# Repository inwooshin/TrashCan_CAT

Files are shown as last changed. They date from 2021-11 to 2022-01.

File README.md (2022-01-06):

# Trash Can   

## 목차    
[1. 개요](#개요)   
[2. 발표영상](#발표영상)   
[3. 사용 CPU 및 센서](#사용-cpu-및-센서)   
[4. 구조 설계](#구조-설계)   
[5, 사용 STL 도면](#사용-stl-도면)   
[6. 외형](#외형)   
[7. 시연 영상](#시연-영상)   
[8. 조원별 역할](#조원별-역할)   

## 개요

push_pull

이 프로젝트는 압축 기능 및 IoT 기능을 사용할 수 있는 쓰레기통인 C.A.T(Can do Anything Trash can) 에 관한 프로젝트이다. WiFi 라이브러리를 사용하고 HTTP 로 ESP8266 과 앱인벤터의 통신이 가능하도록 설계하였다. 그리고 STL 파일으로 Press Hardware 를 수정하여 Scissors Linkage 의 구조로 3D 프린팅 하였으며, Torque 가 부족하기 때문에 기존의 gear 를 1개에서 2개로 사용을 변경하여 Push 와 Pull 이 용이하게 만들었다.
   
## 발표영상
발표영상화면 (https://www.youtube.com/watch?v=RVP99xg6Qa0)   
위의 사진을 클릭하시면 Youtube 링크로 이동합니다.   

## 사용 CPU 및 센서

- **ESP8266**
    
    esp
    
    1. 전체 GPIO 핀을 제어하기 위한 메인보드
    2. Application과 연결하기 위한 WiFi 모듈 내장
    3. 3.3V Power Logic
- **12V Motor Driver**
    
    MotorDriver
    
    1. PWM을 통해서 모터속도 제어 가능
    2. 정전압 역전압으로 양방향 제어 가능
    3. 입력 전압 : 5 ~ 35 V / 동작 전압 : 5V
- **Pololu 50:1 Metal Gearmotor 12V**
    
    gear
)
    
    1. Rack - Pinion 을 구동하기 위한 DC Motor
    2. 구동전압 : 12V / RPM : 200 / Stall Torque : 21kg*cm
    / 정격 설계 : 4.2kg*cm
- **MP3 Module & Speaker**
    
    speaker
    
    1. 3W 전력 / 4Ω Impedance / 직경 : 50mm
    2. 최대 255개의 파일 저장 가능 / 30 Volume Level / 24bit DAC Output
- **DC-DC Convertor**
    
    conv
    
    1. 전원의 12V를 Node MCU 5V 정격 전압으로 강하
    2. 입력 전압 7V ~ 26V / 출력 전압 : 5V / 출력 전류 : 최대 3A
    변환 효율 : 최대 96%
- **단면 PCB 기판**
    
    pcb
    
    1. 브레드 보드를 대체하여 사용
    2. 메인보드 및 각 센서를 납땜하여 사용
- **아크릴 판**
    
    아크릴
    
    1. 본 프로젝트의 외형을 구현, 도면에 따라 재단해서 사용
    - 강판 두께 : 3T(3mm) / 강판 크기 : 500(mm)x500(mm)
- **SR - 04 초음파 센서**
    
    cho
)
    
    1. 동작전압 : 5V / 동작전류 : 15mA / 동작 주파수 : 40Hz
    발생 주파수 : 40kHz / 측정거리 : 2~400cm / 감지각도 : 15
    크기 : 45 x 20 x 15(mm)
- **12V 건전지**
    
    12v
    
    1. 8개입 건전지 CASE를 이용해 [1.5V x 8] 개 12V 전압 입력
- **SG-90**
    
    servo
    
    1. 쓰레기 투입구를 자동으로 열기 위한 Motor
    2. 각도를 0 ~ 180로 변화시키면서 연결된 Wire를 통해 문을 개폐
    3. - Weight : 9g / Torque : 1.3kg*cm(at 4.8V) / RPM : 110

### 구조 설계

- **Hardware**
    - **Scissors Linkage**
        
        ScissorsMechan
        
        구조는 Scissors Mechanism 의 구조로 설계하였다. 위에 부착해서 프레스를 해줘야하는 구조상 크기를 최대한 키우지 않을 수 있게 다리를 안으로 접을 수 있는 구조인 Scissors Mechanism 을 선택했다. 
        
    - **외형 설계**
        
        외형설계
        
    - **회로 설계**
        
        회로설계
        
- **Software**
    - ESP8266 Code (C++)
        
        12V 의 전원을 인가하게 되면 5V 로 변경시켜주는 레귤레이터를 통해서 ESP 8266 이 동작하게 된다. 그 ESP8266 에 달린 입구 부분의 초음파 센서를 확인해서 인접한 거리에 사람이 20Cm 내에 있는지 확인한다. 그리고 내에 있을 경우 입구를 오픈합니다. 또한 쓰레기의 잔량을 확인할 수 있도록 압축 판에 부착한 초음파센서가 쓰레기의 잔량을 재서 20Cm 보다 작으면 압축 동작을 시킬 수 있도록 하였다. 그리고 앱인벤터의 신호를 확인해서 들어오는 Open 이나 Press 그리고 Remain check 같은 잔량 체크를 하는 동작을 수행할 수 있도록 하였다.
        
        소프트웨어플로우차트
        
    - App Inventor
        
        우선 HTTP 의 GET 을 통해서 Compression 의 PRESS 라는 키워드를 넣어서 접속할 경우 해당 키워드에 접속을 주시하고 있던 ESP8266 이 Press 동작을 수행한다. 그리고 이 동작을 한 후 응답을 보내 온전하게 연결이 되고 동작을 수행했는지를 알 수 있도록 하였다. 이 형식으로 Remain check, 딜레이 시간을 조정하는 push 와 pull 의 딜레이 시간을 조정할 수 있도록 하였다.
        
        앱인벤터플로우차트

### 사용 STL 도면

- Linkage 상하단 구조물

stl-1

[https://www.thingiverse.com/thing:3483911](https://www.thingiverse.com/thing:3483911) 의 Scissors Mechanism 도면을 사용하였다. 기존의 것과 다른 것은 아래의 Second Gear 구조물의 Pinion Gear 와 Linkage 상단의 Rack Gear 의 align 을 맞출 수 있도록 수정하였다.

- Second Gear 구조물

stl-2

[https://www.thingiverse.com/thing:677144](https://www.thingiverse.com/thing:677144) 의 도면을 수정하여 사용하였다. 원도면과 Second Gear Holder 가 굉장히 다른 모양이다. 이것은 Linkage 의 도면과 부착하는 부분이 없기 때문에 고정해줄 수 있는 부분을 만들어서 부착해주었고 두번째 기어를 고정하는 부분을 위로 Shift 시켜서 수정했기 때문이다. 그리고 부족한 토크로인한 기어비를 3:1 로 최대로 주기 위해서 조금 더 수정하고 기어와의 align 을 수정하였다.

## 외형

- 정면
    
    전면
    
- 후면
    
    후면

- 측면
    
    측면

## 시연 영상

- Push n Pull

push_pull   
- 앱인벤터로 Press n Pull

앱인벤터푸시

- 외부 사용자 감지 시

open

- 쓰레기통 남은량 감지
    - 전부 비어있을 때
    
    remainCheck_full
    
    - 조금만 차있을 때
    
    remainCheck_half

## 조원별 역할

- 신인우(조장)
    - 전체 코드 구현
    - 하드웨어 설계
    - 부품 선정
    - STL 도면 수정
- 김홍민
    - 하드웨어 설계
    - 부품 선정
    - 외형 설계
    - 음성파일 제작
- 유건환
    - 외형 설계
    - PCB 납땜
    - 외형에 하드웨어 부착
    - 앱인벤터 제작

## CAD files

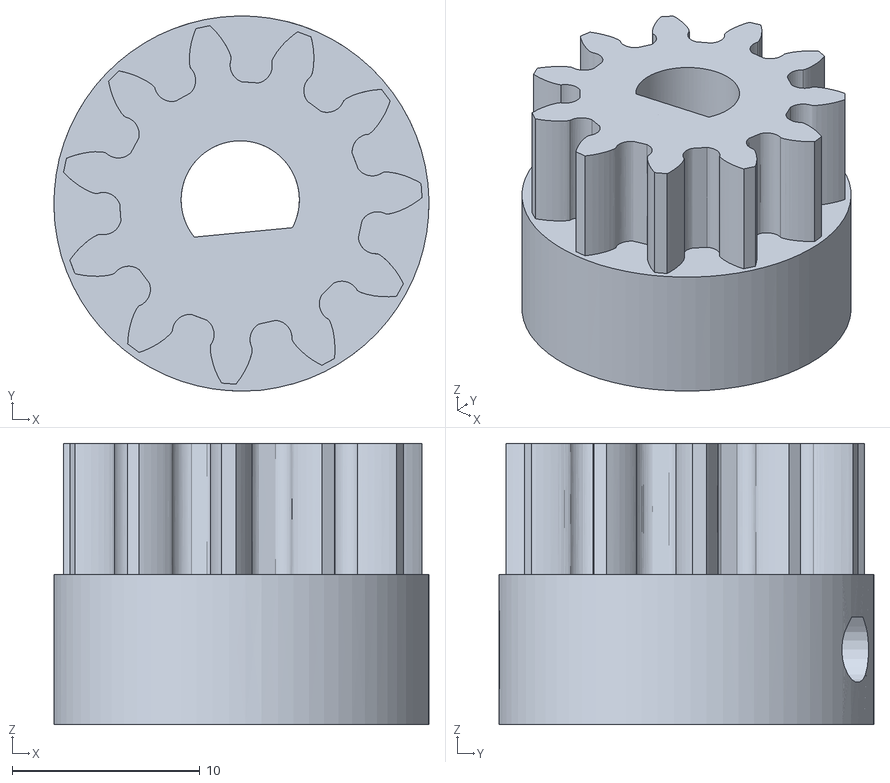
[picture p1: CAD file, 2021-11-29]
stl/wide_small_gear.stl
20.0 x 20.0 x 15.0

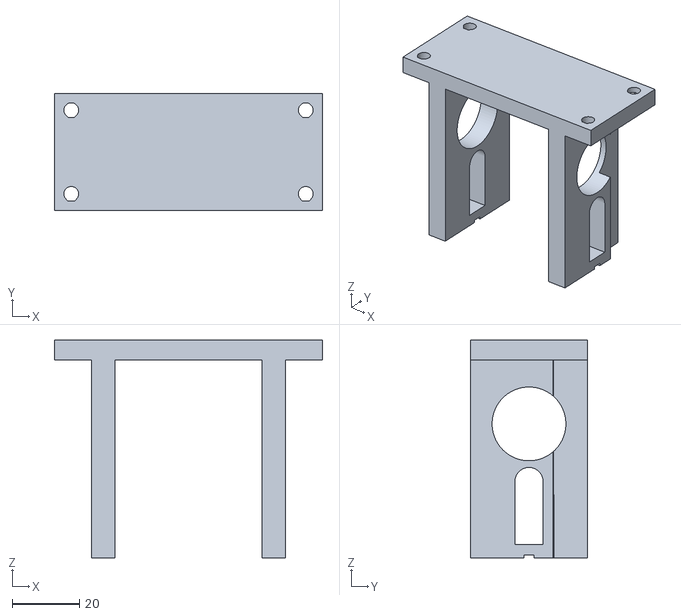
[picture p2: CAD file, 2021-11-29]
stl/Top.stl
80.0 x 35.0 x 65.0

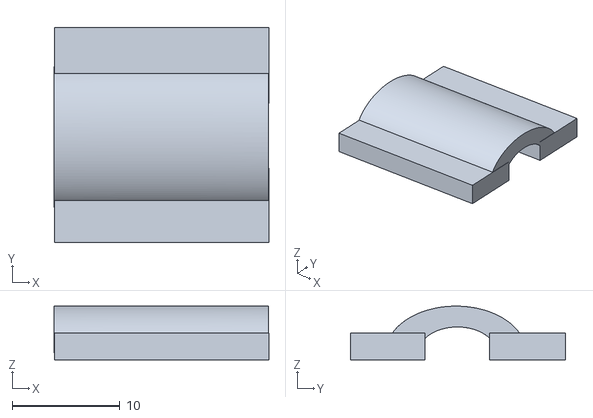
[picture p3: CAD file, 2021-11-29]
stl/thread.stl
20.0 x 20.0 x 5.00

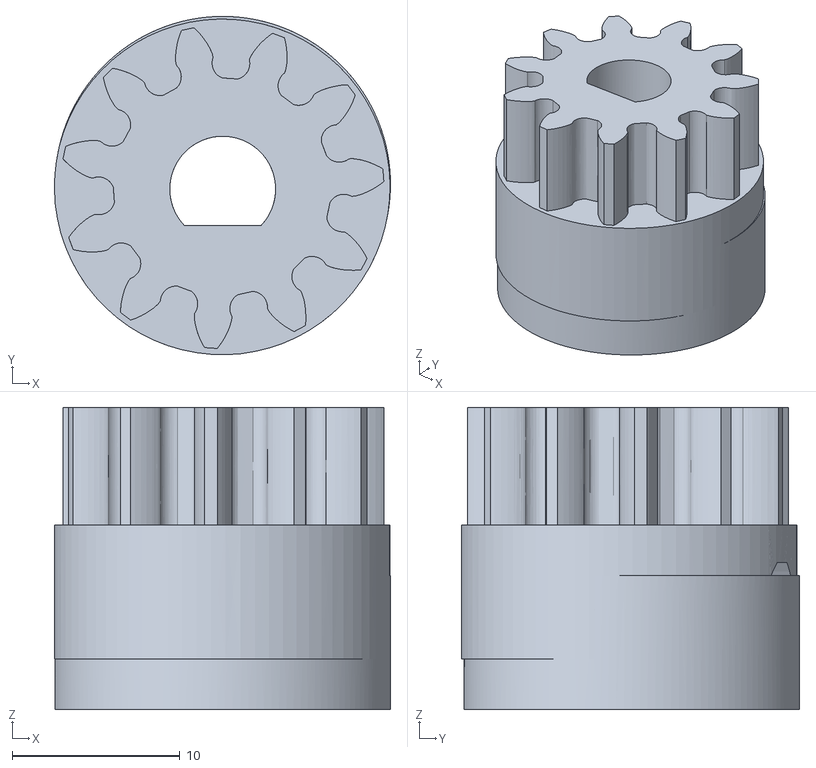
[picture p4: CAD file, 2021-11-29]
stl/small_gear_upversion.stl
20.0 x 20.2 x 18.0

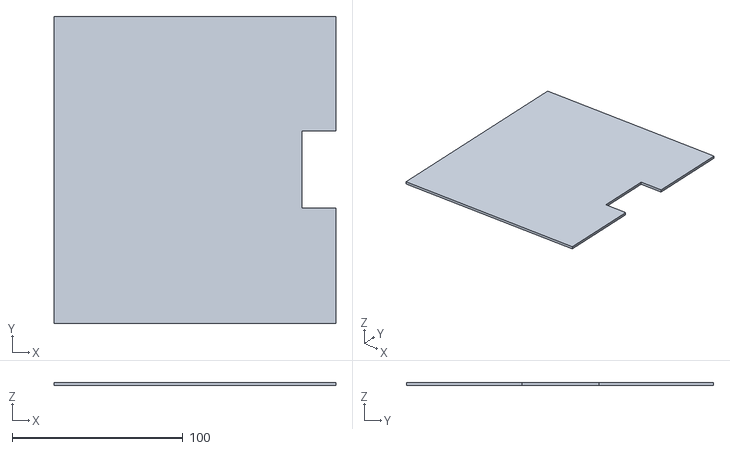
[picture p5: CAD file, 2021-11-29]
stl/press_board.stl
165.1 x 180.0 x 2.00

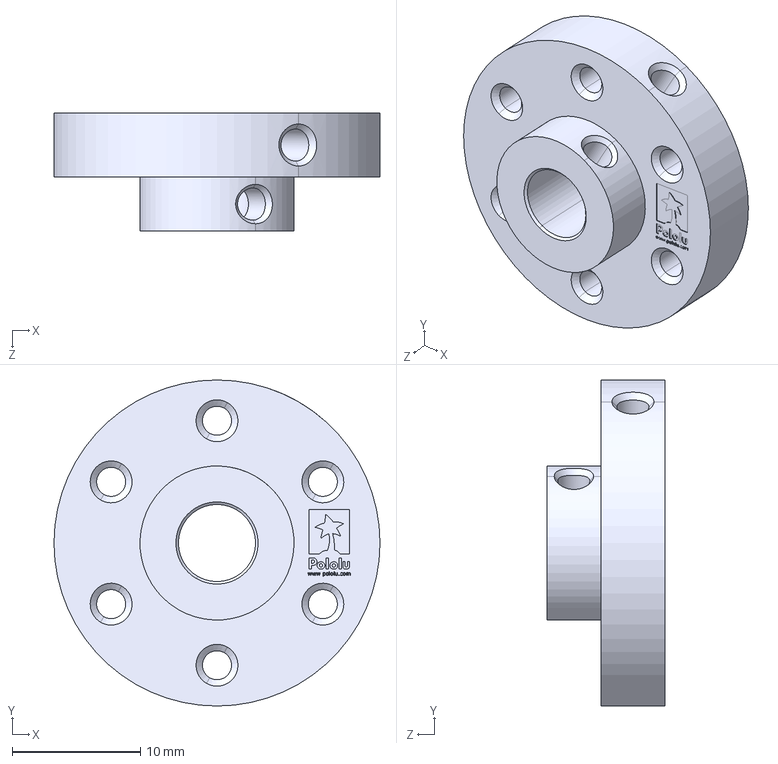
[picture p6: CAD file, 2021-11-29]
stl/pololu-universal-aluminum-mounting-hub-for-6mm-shaft-4-40-holes.step
25.4 x 25.4 x 9.20 mm

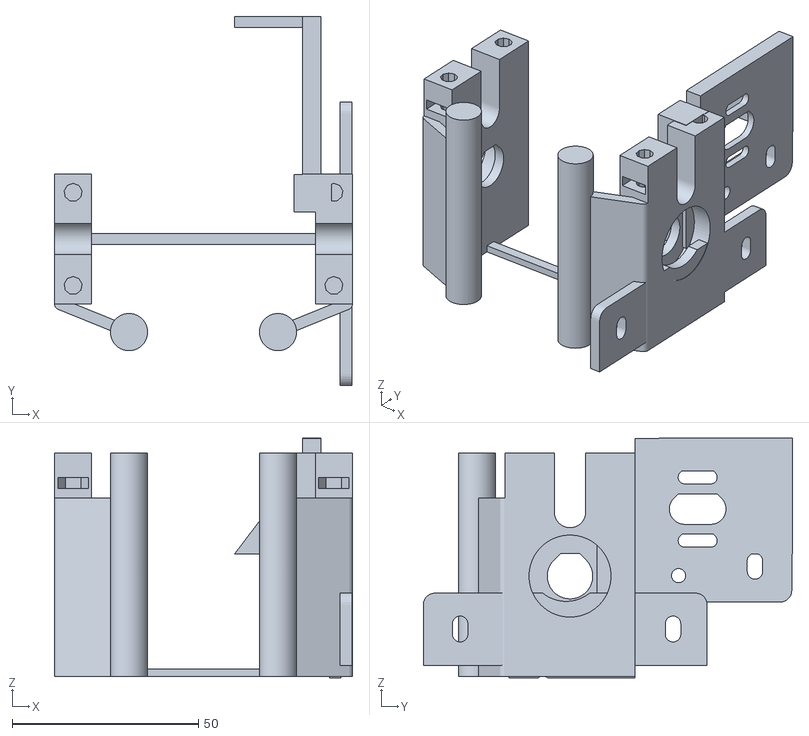
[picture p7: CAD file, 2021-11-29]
stl/newGearHolder.stl
80.0 x 99.2 x 64.3

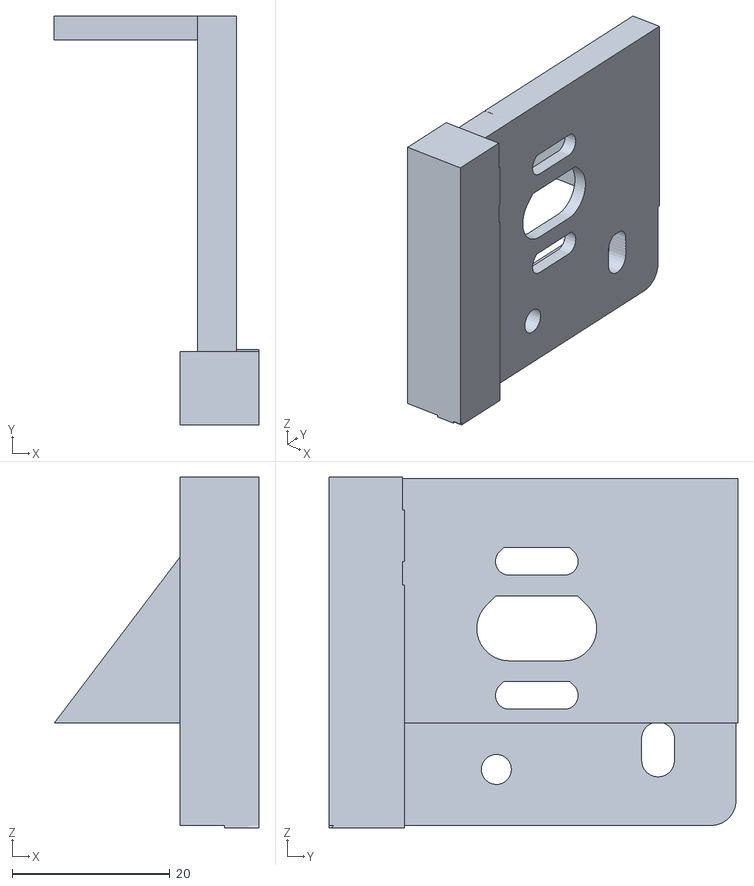
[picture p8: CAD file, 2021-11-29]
stl/floatingGearHolder.stl
25.9 x 51.9 x 44.5

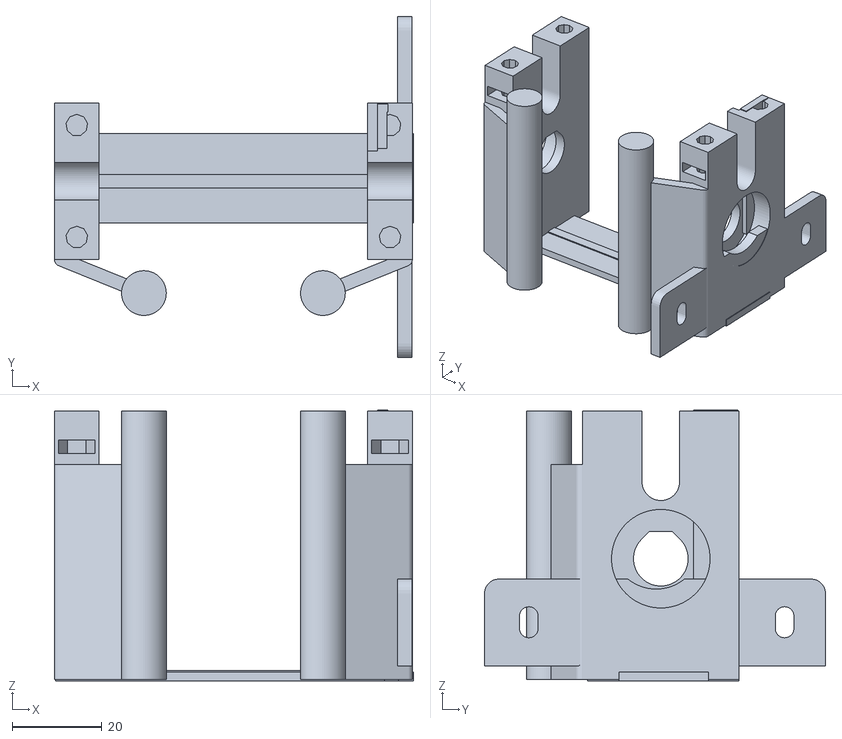
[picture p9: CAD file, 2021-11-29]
stl/braket_one_gear.stl
80.3 x 76.2 x 60.5

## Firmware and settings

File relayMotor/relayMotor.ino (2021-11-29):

#include "Servo.h"
#define RelayPlusPin D1
#define RelayMinusPin D2
#include "SoftwareSerial.h"
#include "DFRobotDFPlayerMini.h"
#include <ESP8266WiFi.h>
#include <ESP8266HTTPClient.h>

//openECHO 나중에 바꿔야함!!

int pushTRIG = D7;    // 트리거 핀 선언
int pushECHO = D6;    // 에코 핀 선언
int openTRIG = D4;    // SD3 나중에 바꿔야함
int openECHO = D5;
int servoPin = D8;

//확정
int servoStart = 0, servoEnd = 90, servoDelay = 5000;

//D3,4-> D4에서 input 으로 설정해주면 에러가 나는 것 같다!(input 설정이 안되는 듯)
//D3 도 output trig 했는데 안됨
//빨강이 위, 갈색이 아래

//
int Clock = 1, pushDelayTime = 230, pullDelayTime = 335, count = 0;
int pushPower = 900, pullPower = 1020;
int distanceDelayTime = 100;
int vol = 25;

const char *ssid = "INS_phone";
const char *password = "kkkkkkkk";

IPAddress ip (192, 168, 119, 101); // 연결할, 고정 IP 주소
IPAddress gateway (192, 168, 119, 135); // 게이트웨이 주소
IPAddress subnet (255, 255, 255, 0); // 서브마스크 주소
WiFiServer server(80);
WiFiClient client;
Servo myServo;

SoftwareSerial mySoftwareSerial(3, 1); // RX, TX
DFRobotDFPlayerMini myDFPlayer;

int countDistance(int modeChoice, int runMode);

//모터 동작 멈추기
void stop(){
  digitalWrite(RelayPlusPin, LOW);
  digitalWrite(RelayMinusPin, LOW);  
}

//모터 press
void push(){
  analogWrite(RelayPlusPin,1024);
  digitalWrite(RelayMinusPin,LOW); // 회전
  delay(pushDelayTime);
  stop();
}

//모터 pull
void pull(){
  digitalWrite(RelayPlusPin,LOW); 
  analogWrite(RelayMinusPin,1024);
  delay(pullDelayTime);
  stop();
}

//모터 사이클 동작
void motorCycle(){
  //push 음성안내 음성 출력
  myDFPlayer.play(1);
  delay(2500);
  Serial.println("push");
  push();
      
  delay(2000);
  
  //pull 음성안내 출력
  myDFPlayer.play(2);
  delay(1000);
  Serial.println("pull");
  pull();
}

void servoRun(){
  //문 Open 음성안내 출력
  myDFPlayer.play(4);
  
  myServo.write(servoStart);
  delay(servoDelay);
  myServo.write(servoEnd);
}

int countDistance(int modeChoice, int runMode){
  //modeChoice - mode == 0 -> push 거리, mode == 1 open 거리
  //runMode - runMode == 0 -> 작동 x, runMode == 1 -> 작동 o
  int TRIG = 0, ECHO = 0;
  
  //
  if(modeChoice == 0){ 
    Serial.println("press Distance");
    TRIG = pushTRIG;
    ECHO = pushECHO;
  }
  else{ 
    Serial.println("Open Distance");
    TRIG = openTRIG;
    ECHO = openECHO;
  }
  
  //open 일 경우 0, press 일 경우 1
  long duration, distance;
  digitalWrite(TRIG, LOW);
  delayMicroseconds(2);
  digitalWrite(TRIG, HIGH);
  delayMicroseconds(10);
  digitalWrite(TRIG, LOW);

  //물체에 반사되어돌아온 초음파의 시간을 변수에 저장합니다.
  duration = pulseIn (ECHO, HIGH); 
  distance = duration * 17 / 1000; 

  //측정된 물체로부터 거리값(cm값)을 보여줍니다.
  Serial.print(distance); 
  Serial.println(" Cm");

  delay(distanceDelayTime);
  count++;


  //프레스동작 - 0, 오픈동작 - 1
  if(distance < 20 && runMode == 1){ 
    if(modeChoice == 0){
      
      motorCycle();
    }
    else{
      stop();
      
      servoRun();
    }
  }
  
  return distance;
}

void setup() {
  // put your setup code here, to run once:
  Serial.begin(9600);
  delay(10);
  pinMode(RelayPlusPin, OUTPUT);
  pinMode(RelayMinusPin, OUTPUT);

  Serial.println("1. push, 2.stop, 3.pull");
  Serial.println("qw : push +-, ty : pull +-");

  stop();
  
  pinMode(pushTRIG, OUTPUT);    // 트리거 핀 출력으로 선언
  pinMode(pushECHO, INPUT);     // 에코 핀 입력으로 선언

  pinMode(openTRIG, OUTPUT);    // 트리거 핀 출력으로 선언
  pinMode(openECHO, INPUT);     // 에코 핀 입력으로 선언

  myServo.attach(servoPin);

  WiFi.disconnect (true);
  delay(1000);

  Serial.print("Connecting...");
  Serial.println(ssid);
  WiFi.config (ip, gateway, subnet);
  WiFi.begin(ssid, password);
  while(1)
  {
    if(WiFi.status()==WL_CONNECTED)break;
    Serial.print(".");
    delay(500);
  }
  Serial.printf("Connected!\r\n");

  server.begin();
  Serial.println("server Start");

  Serial.println(WiFi.localIP());
//
  if (!myDFPlayer.begin(Serial)) {
    Serial.println("Unable to begin:");
    Serial.println("1.Please recheck the connection!");
    Serial.println("2.Please insert the SD card!");
  }
  Serial.println("DFPlayer Mini online.");
   
  myDFPlayer.volume(vol);
}

int whatMode = 1; //mode가 0 이면 push 초음파, 1 이면 open 초음파
//

void loop() {
  //1. 잔량
  //2. 문 열기
  //3. 압축 올리기
  //4. 압축 시작
  //modeChoice - mode == 0 -> push 거리, mode == 1 open 거리
  //runMode - runMode == 0 -> 작동 x, runMode == 1 -> 작동 o

  //press 부분 거리재기, runMode true
  countDistance(0, 1);

//  //open 부분 거리재기. runMode true
  countDistance(1, 1);
  
  client = server.available();
  if(client){
    if(client.connected())
    {
      //Serial.println("connect sucess");
      }
    else
    {
    Serial.println("접속 대기 중...");
    delay(500);
    client.stop();
    }
  }

// Response & Request Configure //
  //char* IP_Address = WiFi.localIP().toString().;
  String str1 = "HTTP/1.1 200 OK\r\nContent-Type: text/html\r\n\r\n \r\n\r\n PRESS ON!";

  Serial.println("readString start : ");
  String REQ = client.readStringUntil('\r');
  Serial.println("readString end : ");
  Serial.println(REQ);

// WiFi Control Section //
  if(REQ.indexOf("/WIFI/1") != -1)
  {
    Serial.println("WiFi_Imform Submit");
    client.printf("HTTP/1.1 200 OK\r\nContent-Type: text/html\r\n\r\n \r\n\r\n WIFI");
    delay(20);
    client.printf("HTTP/1.1 200 OK\r\nContent-Type: text/html\r\n\r\n \r\n\r\n IP Adress is %s SSID is %c", WiFi.localIP().toString().c_str(), ssid);
    }
    
// REMAIN Check Section//
  else if(REQ.indexOf("/REMAIN/1") != -1)
  {
    int dis = countDistance(0,0);
    Serial.println(dis);
    client.printf("HTTP/1.1 201 OK\r\nContent-Type: text/html\r\n\r\n \r\n\r\n %d", dis);
    }
    
// Compression Control Section //      
  else if(REQ.indexOf("/PRESS/1") != -1){
    motorCycle(); 
    client.print(str1);
  }

  else if(REQ.indexOf("/PUSH/1") != -1){
    push();
    client.print("HTTP/1.1 200 OK\r\nContent-Type: text/html\r\n\r\n \r\n\r\n PUSH!");
  }

  else if(REQ.indexOf("/PULL/1") != -1){
    pull();
    client.print("HTTP/1.1 200 OK\r\nContent-Type: text/html\r\n\r\n \r\n\r\n PULL!");
  }
  

// Push&Pull Power Control Section //      
  else if(REQ.indexOf("/PULLUP/1") != -1){
  pullDelayTime += 50;
  Serial.println(pullDelayTime);
  client.printf("HTTP/1.1 200 OK\r\nContent-Type: text/html\r\n\r\n \r\n\r\n Press pull power %d", pullDelayTime);
  servoRun();

  
  } //PULL UP
  
  else if(REQ.indexOf("/PULLDOWN/1") != -1)
  {
  pullDelayTime -= 50;
  Serial.println(pullDelayTime);
  client.printf("HTTP/1.1 200 OK\r\nContent-Type: text/html\r\n\r\n \r\n\r\n Press pull power %d", pullDelayTime);
  }
  
  else if(REQ.indexOf("/PUSHUP/1") != -1){
  pushDelayTime += 50;
  Serial.println(pushDelayTime);
  client.printf("HTTP/1.1 200 OK\r\nContent-Type: text/html\r\n\r\n \r\n\r\n Press pull power %d", pushDelayTime);
  }
  
  else if(REQ.indexOf("/PUSHDOWN/1") != -1)
  {
  pushDelayTime += 50;
  Serial.println(pushDelayTime);
  client.printf("HTTP/1.1 200 OK\r\nContent-Type: text/html\r\n\r\n \r\n\r\n Press pull power %d", pushDelayTime);
  }

// Volume Control Section //
  else if(REQ.indexOf("/VOLU/1") != -1)
  {
  vol += 5;
  if(vol > 30) vol = 30;
  
  Serial.println(vol);
  client.printf("HTTP/1.1 200 OK\r\nContent-Type: text/html\r\n\r\n \r\n\r\n Volume Up %d", vol);
  }
  
  else if(REQ.indexOf("/VOLD/1") != -1)
  {
  vol -= 5;
  if(vol <0) vol = 0;
  Serial.println(vol);
  client.printf("HTTP/1.1 200 OK\r\nContent-Type: text/html\r\n\r\n \r\n\r\n Volume Down %d", vol);
  } 

  //버튼 누르면 오픈하기
  else if(REQ.indexOf("/OPEN/1") != -1)
  {
  servoRun();
  Serial.println("open");
  client.printf("HTTP/1.1 200 OK\r\nContent-Type: text/html\r\n\r\n \r\n\r\n open");
  } 

  // when Request Fail //      
  client.flush();

  if(Serial.available()){
      String inString = Serial.readStringUntil('\n');
      Serial.println(inString);
      if(inString == "1"){
        push();
        Serial.println("push");
      }
      else if(inString == "w"){
        pull();
        Serial.println("pull");
      }
  }
}

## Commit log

2021-11-29 main 코드 추가
    1. press 부분 초음파 센서 20cm 거리 내 일 경우 press n pull 동작
    2. 입구 부분 초음파 센서 20cm 거리 내 일 경우 입구 open 동작
    3. 앱인벤터 palling 중 HTTP GET 호출 시 접속한 Keyword 에 따른 Push Pull 및 동작 수행
2021-11-29 Readme 추가
2021-11-29 Readme 목차 추가
2021-11-29 큰 기어 고정대 도면
    [braket_one_gear.stl]
2021-11-29 작은 기어 도면
    큰 기어와 작은 기어를 맞춰서 랙기어를 돌려야하는데 원 도면에서는 작은 기어 부분이 랙기어에 맞닿게 되어서 띄우는 방식으로 수정하였다.
    [floatingGearHolder.stl]
2021-11-29 두가지 기어를 합친 고정대
    [newGearHolder.stl]
2021-11-29 Motor Mountain Hub
    보통 알루미늄의 허브를 많이 사용하지만, 해외배송이고 구매가 오래걸리는 점을 고려해서 Mountain Hub 를 3d printing 해서 사용하였다.
    [pololu-universal-aluminum-mounting-hub-for-6mm-shaft-4-40-holes.step]
2021-11-29 실질적으로 압축할 때 쓰레기와 닿는 판
    [press_board.stl]
2021-11-29 작은 pinion gear 수정
    작은 기어의 높이를 높혀서 나사로 고정할 수 있는 면을 늘려 부러지지 않고 꽉 조일 수 있도록 하였다.
    [small_gear_upversion.stl]
2021-11-29 문을 열어주는 부분의 이음새
    [thread.stl]
2021-11-29 합친 두개의 기어를 상판에 고정시킬 고정대
    [Top.stl]
2021-11-29 기어의 입구를 모터에 맞게 수정
    [wide_small_gear.stl]
2021-11-29 Readme 조원 기여 수정
2021-11-29 발표영상 기재
2021-11-29 발표 유투브 링크 변경
2021-11-29 발표 영상 이미지 변경
2021-12-29 발표영상 목차 수정
2022-01-06 trashcan 리드미 수정
